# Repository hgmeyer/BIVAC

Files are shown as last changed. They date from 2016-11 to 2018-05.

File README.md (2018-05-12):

# BIVAC
While navigating their environments it is essential for autonomous mobile systems to actively avoid collisions with obstacles. Flying insects perform this behavioural task with ease relying mainly on information the visual system provides. BIVAC (Bio-Inspired Visual Avoidance of Collisions) is a low-cost collision avoidance system based on the extraction of nearness information from visual motion. The system allows an autonomous mobile agent to navigate in cluttered environments while actively avoiding obstacles.

**Please note:** This is the repository for a project that will be hosted on [hackaday.io](http://hackaday.io/). Please visit the [project page](https://hackaday.io/project/13301-bivac-bio-inspired-visual-collision-avoidance/) for more information.

<br />This work is licensed under a <a rel="license" href="http://creativecommons.org/licenses/by-sa/4.0/">Creative Commons Attribution-ShareAlike 4.0 International License</a>.

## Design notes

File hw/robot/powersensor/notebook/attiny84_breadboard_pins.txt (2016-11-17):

# I2C
SDA   -   E25
SCL   -   E26

# Digital
PB0   -   E27
PB1   -   E28

# Voltage measurement
12V   -   F25
5V    -   F26
3.3V  -   F27
1.8V  -   F28

# Current measurement
C_A   -   F29
C_B   -   F30

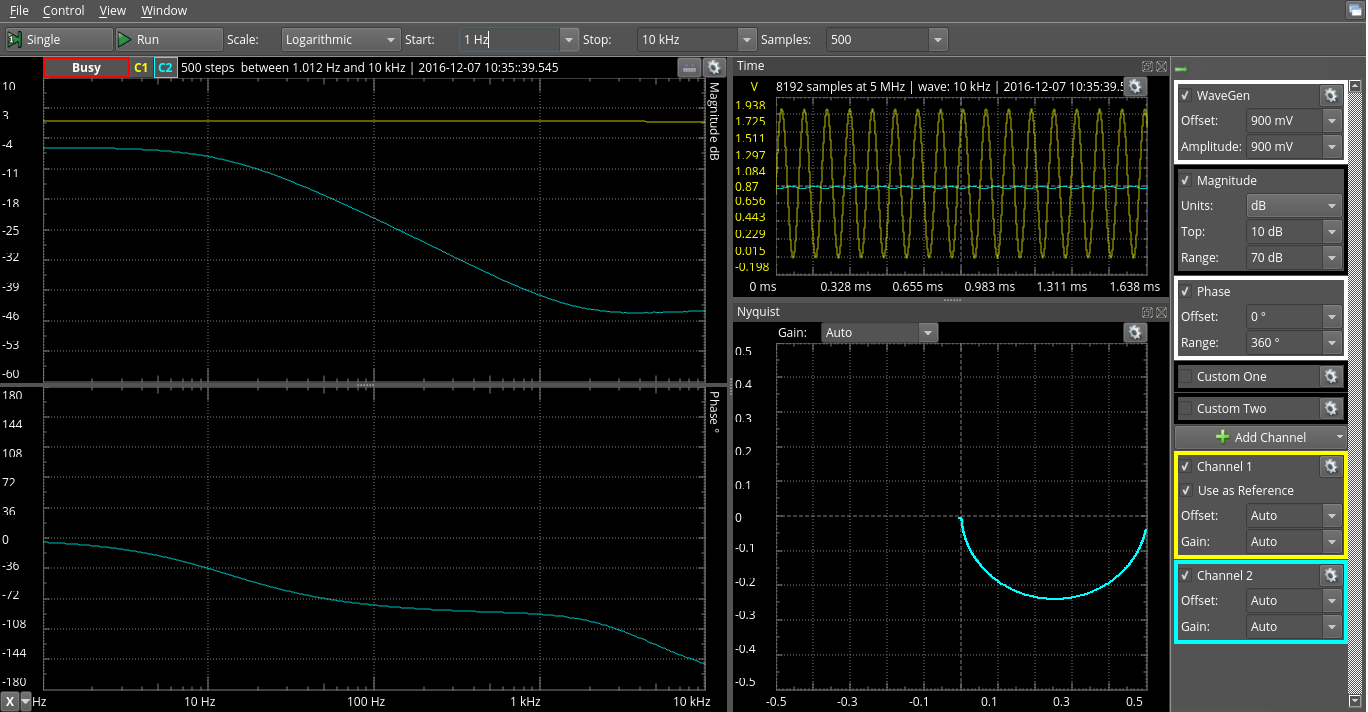
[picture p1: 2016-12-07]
hw/robot/powersensor/hw/analysis/input_stage.png

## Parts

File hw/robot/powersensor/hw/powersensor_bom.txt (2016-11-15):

Qty Value    Device             Package  Parts                Description                 PROD_ID (Reichelt)
5            M01PTH             1X01     J3, J4, J5, J6, J9   Header 1
1            M05PTH             1X05     J7                   Header 5
1            M06SILK_FEMALE_PTH 1X06     J8                   Header 6
1   1.8V     LED0603            LED-0603 D4                   LEDs                        LY L29K
1   100nF    CAP0603-CAP        0603-CAP C5                   Capacitor                   X7R-G0603 100N
4   10u      CAP0603-CAP        0603-CAP C1, C2, C3, C4       Capacitor                   GRM188R60J106ME47D (Conrad)
1   13k      RESISTOR0603-RES   0603-RES R1                   Resistor                    RND 0603 1 13K
5   1k1      RESISTOR0603-RES   0603-RES R2, R5, R8, R10, R11 Resistor                    RND 0603 1 1,1K
1   2k7      RESISTOR0603-RES   0603-RES R7                   Resistor                    RND 0603 1 2,7K
1   3.3V     LED0603            LED-0603 D3                   LEDs                        LO L29K
2   1k       RESISTOR0603-RES   0603-RES R17, R18             Resistor                    (optional)
1   4k7      RESISTOR0603-RES   0603-RES R4                   Resistor                    RND 0603 1 4,7K
1   5V       LED0603            LED-0603 D2                   LEDs                        LS L29K
4   750R     RESISTOR0603-RES   0603-RES R3, R6, R9, R12      Resistor                    RND 0603 1 750
1   ATTINY84 ATTINY84           SO14     U$1                  Atmel 14-pin 8kB flash uC   ATTINY 84A-SSU
1   I2C      PINHD-1X3/90       1X03/90  J2                   PIN HEADER
1   ISP      AVR_SPI_PRG_6PTH   2X3      J1                   AVR ISP 6 Pin
1   V_BAT    LED0603            LED-0603 D1                   LEDs                        LG L29K
1   560R     RESISTOR0603-RES   0603-RES R13                  Resistor                    SMD-0603 560
1   180R     RESISTOR0603-RES   0603-RES R14                  Resistor                    SMD-0603 180
1   82R      RESISTOR0603-RES   0603-RES R15                  Resistor                    SMD-0603 82
1   0R       RESISTOR0603-RES   0603-RES R16                  Resistor                    SMD-0603 0

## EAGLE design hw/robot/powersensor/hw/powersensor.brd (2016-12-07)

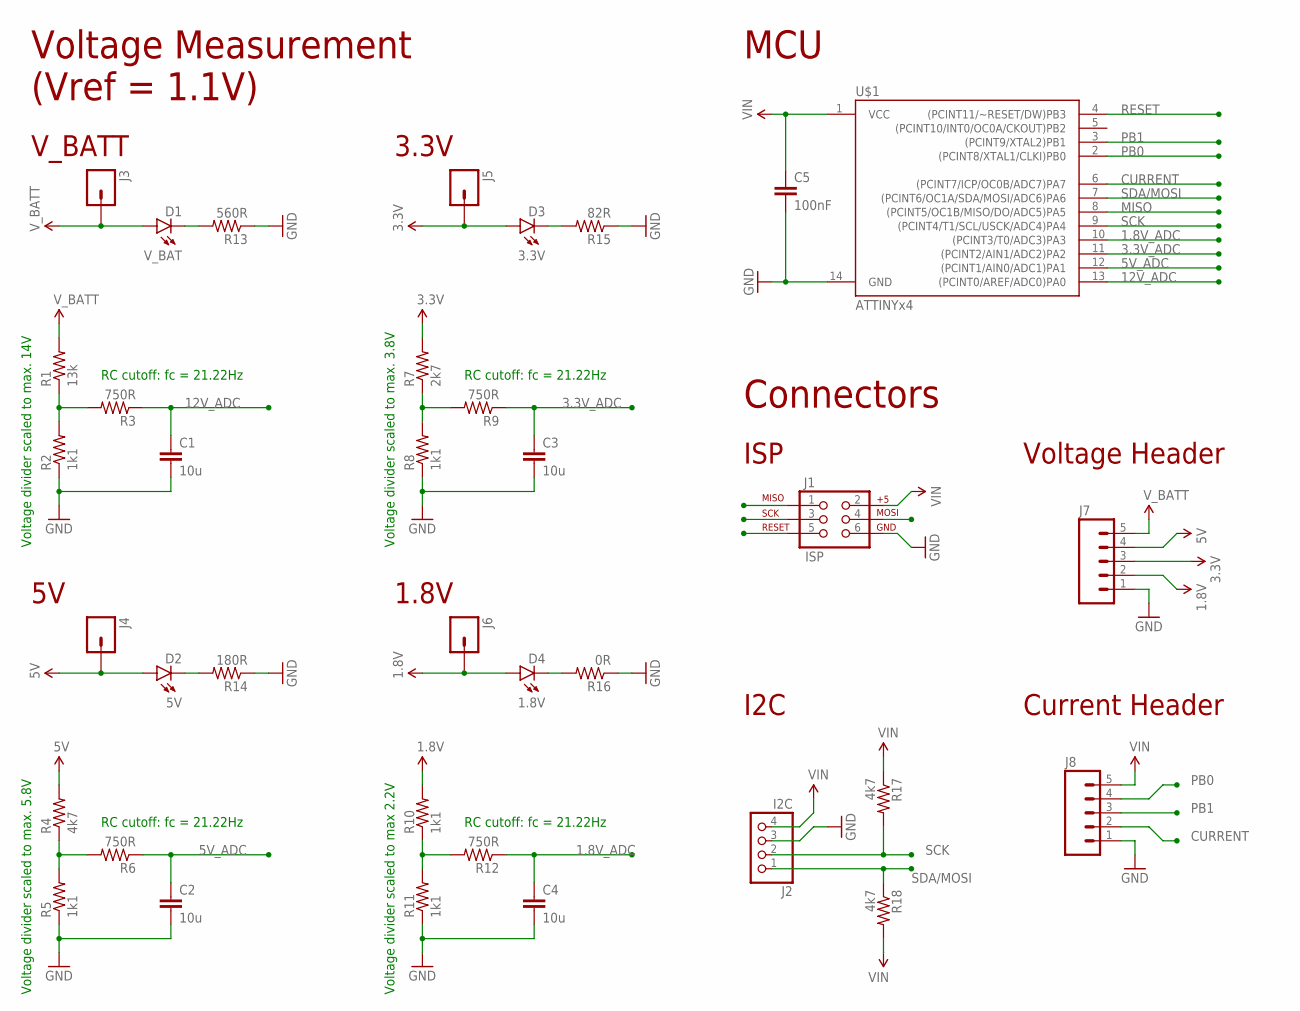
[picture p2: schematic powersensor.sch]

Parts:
C1, C2, C3, C4: 10u; 0603-CAP
C5: 100nF; 0603-CAP
D1: V_BAT; LED-0603
D2: 5V; LED-0603
D3: 3.3V; LED-0603
D4: 1.8V; LED-0603
J1: ISP; 2X3
J2: I2C; 1X04/90
J3, J4, J5, J6: M01PTH; 1X01
J7, J8: M05PTH; 1X05
R1: 13k; 0603-RES
R2, R5, R8, R10, R11: 1k1; 0603-RES
R3, R6, R9, R12: 750R; 0603-RES
R4, R17, R18: 4k7; 0603-RES
R7: 2k7; 0603-RES
R13: 560R; 0603-RES
R14: 180R; 0603-RES
R15: 82R; 0603-RES
R16: 0R; 0603-RES
U$1: ATTINYx4; SO14

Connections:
1.8V: D4.A, J6.1, J7.2, R10.2
1.8V_ADC: C4.1, R12.1, U$1.10 ((PCINT3/T0/ADC3)PA3)
3.3V: D3.A, J5.1, J7.3, R7.2
3.3V_ADC: C3.1, R9.1, U$1.11 ((PCINT2/AIN1/ADC2)PA2)
5V: D2.A, J4.1, J7.4, R4.2
5V_ADC: C2.1, R6.1, U$1.12 ((PCINT1/AIN0/ADC1)PA1)
12V_ADC: C1.1, R3.1, U$1.13 ((PCINT0/AREF/ADC0)PA0)
CURRENT: J8.2, U$1.6 ((PCINT7/ICP/OC0B/ADC7)PA7)
GND: C1.2, C2.2, C3.2, C4.2, C5.2, J1.6, J2.3, J7.1, J8.1, R2.1, R5.1, R8.1, R11.1, R13.1, R14.1, R15.1, R16.1, U$1.14 (GND)
MISO: J1.1, U$1.8 ((PCINT5/OC1B/MISO/DO/ADC5)PA5)
unnamed: R1.1, R2.2, R3.2
unnamed: R4.1, R5.2, R6.2
unnamed: R7.1, R8.2, R9.2
unnamed: R10.1, R11.2, R12.2
unnamed: D1.C, R13.2
unnamed: D2.C, R14.2
unnamed: D3.C, R15.2
unnamed: D4.C, R16.2
PB0: J8.4, U$1.2 ((PCINT8/XTAL1/CLKI)PB0)
PB1: J8.3, U$1.3 ((PCINT9/XTAL2)PB1)
RESET: J1.5, U$1.4 ((PCINT11/~RESET/DW)PB3)
SCK: J1.3, J2.2, R17.2, U$1.9 ((PCINT4/T1/SCL/USCK/ADC4)PA4)
SDA/MOSI: J1.4, J2.1, R18.1, U$1.7 ((PCINT6/OC1A/SDA/MOSI/ADC6)PA6)
VIN: C5.1, J1.2, J2.4, J8.5, R17.1, R18.2, U$1.1 (VCC)
V_BATT: D1.A, J3.1, J7.5, R1.2

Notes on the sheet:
Voltage divider scaled to max. 14V
Voltage divider scaled to max. 3.8V
Voltage divider scaled to max 2.2V
Voltage divider scaled to max. 5.8V
V_BATT
3.3V
1.8V
Voltage Measurement (Vref = 1.1V)
MCU
ISP
Connectors
I2C
Voltage Header
Current Header
RC cutoff: fc = 21.22Hz

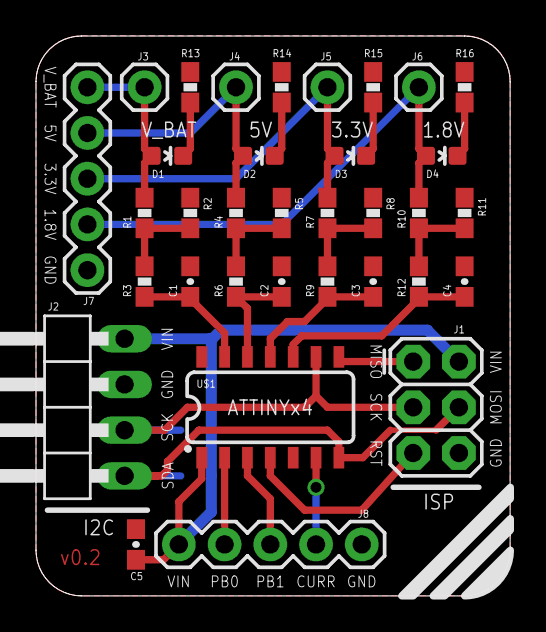
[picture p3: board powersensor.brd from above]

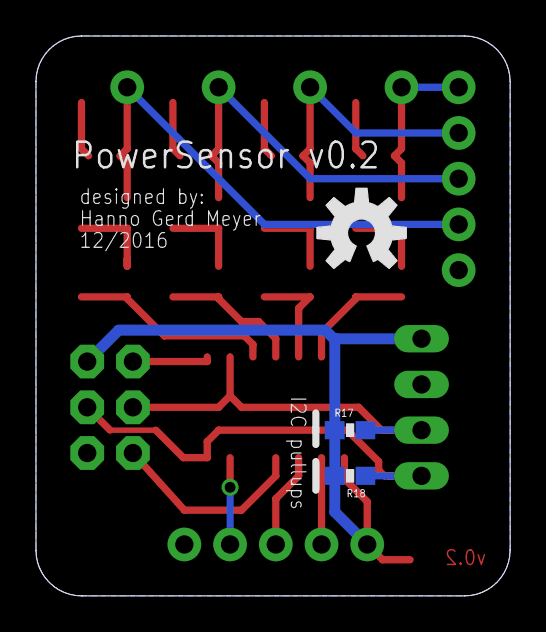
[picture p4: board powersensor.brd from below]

Board: 2 copper layers, 26.3 x 31.1 mm, 37 parts (3 on the bottom side), 25 nets.

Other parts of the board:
U$3: OSHW-LOGO-M

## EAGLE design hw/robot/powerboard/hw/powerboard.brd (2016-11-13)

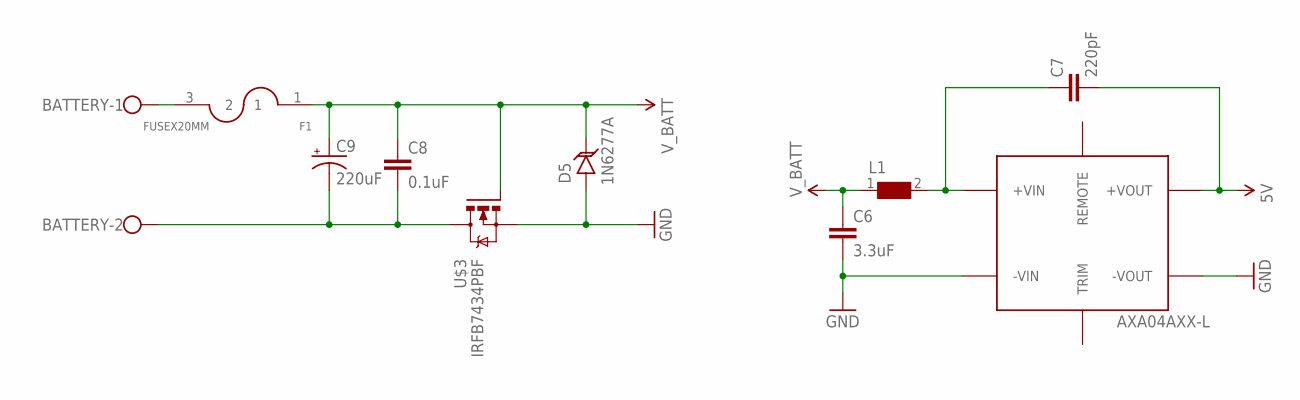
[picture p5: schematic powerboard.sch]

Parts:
BATTERY: W237-102
C6: 3.3uF; 1210
C7: 220pF; C1808
C8: 0.1uF; 0603-CAP
C9: 220uF; PANASONIC_G
D5: 1N6277A
F1: FUSEX20MM; FUSE_5MM
L1: WE-HCI-744314650_7030/7040/7050; WE-HCI_7030/7040/7050
U$2: AXA04AXX-L
U$3: IRFB7434PBF

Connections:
5V: C7.2, U$2.+VOUT
GND: C6.2, D5.A, U$2.-VIN, U$2.-VOUT, U$3.SOURCE (S)
unnamed: C7.1, L1.2, U$2.+VIN
unnamed: BATTERY.1, F1.3 (2)
unnamed: BATTERY.2, C8.2, C9.-, U$3.DRAIN (D)
V_BATT: C6.1, C8.1, C9.+, D5.C, F1.1, L1.1, U$3.GATE (G)

Board: 2 copper layers, 10 parts (0 on the bottom side), 6 nets, no tracks yet.

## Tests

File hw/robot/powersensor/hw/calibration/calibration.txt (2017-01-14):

5V transfer function:
8.755e-05 x + 0.0005361
a: 0.000536051312588, b: 8.75483919078e-05

3.3V transfer function:
5.727e-05 x - 0.00478
a: -0.00478023205199, b: 5.72741545385e-05

1.8V transfer function
3.297e-05 x + 0.008651
a: 0.00865060511459, b: 3.29668929132e-05

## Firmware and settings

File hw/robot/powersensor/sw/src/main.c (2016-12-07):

/*
 * PowerSensor v0.2 firmware
 * Copyright (C) 2016 Hanno Gerd Meyer <hanno@neuromail.de>
 *
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
 * You should have received a copy of the GNU General Public License along with
 * this program.  If not, see <http://www.gnu.org/licenses/>.
 */

#include <avr/io.h>
#include <avr/interrupt.h>
#include <util/delay.h>
#include <usiTwiSlave.h>

#ifndef DEBUG
#define DEBUG 0
#endif

// Define I2C adress of slave (Note: LSB is the I2C r/w flag and must not be used for addressing!)
#define SLAVE_ADDR  0b00001000  // 0x04

// The number of ADC channels to be multiplexed
#define ADC_N   5

// ADC channel and index variables
uint8_t adc_channels[ADC_N] = {0, 1, 2, 3, 7}; // PA0, PA1, PA2, PA3, PA7
uint8_t adc_index = 0;

// ADC buffer
uint16_t adc_buffer;
uint8_t adc_lowbyte;

void initTimer(void)
{
        // Set timer to CTC mode
        TCCR0A |= (1 << WGM01);

        // Set prescaler to 64
        TCCR0B |= (1 << CS01)|(1 << CS00);

        // Initialize counter
        TCNT0 = 0;

        // Set compare value corresponding to 500Hz (100Hz per Channel)
        OCR0A = 250;

        // Enable compare interrupt
        TIMSK0 |= (1 << OCIE0A);
}

void initADC(void)
{
        // Set reference voltage to 1.1V
        ADMUX |= (1 << REFS1);

        // Clear MUX0:5 and set adc channel according to current index
        ADMUX = (ADMUX & ~(0x3F)) | (adc_channels[adc_index] & 0x3F);

        // Enable ADC
        ADCSRA |= (1 << ADEN);

        // Set prescaler to 64 (125kHz)
        ADCSRA |= (1 << ADPS2) |
                  (1 << ADPS1);
}

ISR (TIM0_COMPA_vect)
{
        // Start ADC measurement
        ADCSRA |= (1 << ADSC);

        if(DEBUG) {
                // Toggle PB0
                PORTB ^= (1 << PB0);
        }
}

int main(void)
{

        if(DEBUG) {
                // Set PB0 and PB1 as output pins
                DDRB |= (1<<PB0) | (1<<PB1);
        }

        // Calibrate clock
        OSCCAL -= 0;

        // Disable interrupts
        cli();

        // Initialize timer
        initTimer();

        // Initialize ADC
        initADC();

        // Enable I2C slave
        usiTwiSlaveInit(SLAVE_ADDR);

        // Enable interrupts
        sei();

// Main loop
        while (1)
        {
                // If ADC measurement has been completed
                if ((ADCSRA & (1 << ADSC)) == 0)
                {
                        if (DEBUG) {
                                // Toggle PB1
                                PORTB ^= (1 << PB1);
                        }

                        // Get low byte of ADC measurement
                        adc_lowbyte = ADCL;

                        // Scale 10 Bit measurement to 16 Bit
                        adc_buffer = (ADCH << 8 | adc_lowbyte) * 64;

                        // Write ADC measurement to buffer
                        txbuffer[adc_index+adc_index] = adc_buffer;
                        txbuffer[adc_index+adc_index+1] = adc_buffer >> 8;

                        // Set ADC index
                        if (adc_index < ADC_N-1) {
                                adc_index += 1;
                        }
                        else{
                                adc_index = 0;
                        }

                        // Clear MUX0:5 and set ADC channel
                        ADMUX = (ADMUX & ~(0x3F)) | (adc_channels[adc_index] & 0x3F);

                        // Wait until next ADC measurement starts
                        while((ADCSRA & (1 << ADSC)) == 0) {}
                }
        }

        return 0;
}

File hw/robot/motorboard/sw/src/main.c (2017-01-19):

#include <avr/io.h>
#include <avr/interrupt.h>
#include <util/delay.h>
#include <usiTwiSlave.h>

// Define I2C adress of slave (Note: LSB is the I2C r/w flag and must not be used for addressing!)
#define SLAVE_ADDR  0b00001000  // 0x04

/* Initializes 16-Bit Timer1 for generating phase-correct PWM signal on OC1B pin */
void initPWMTimer(void){

        // * Set Timer1 to PWM mode 10: phase-correct, ICR1 defines top
        // * Clear OC1B on Compare Match when upcounting. Set OC1B on Compare Match when downcounting.
        // * Set prescaler to
        TCCR1A |= (1 << COM1B1) | (1 << WGM11);
        TCCR1B |= (1 << WGM13) | (1 << CS11) |(1 << CS10);

        // Set OC1B pin (PA5) as output
        DDRA  |= (1 << PA5);

        // Set Timer1 top to 16-bit MAX
        ICR1 = 0xFFFF;

        // Set duty cycle to 0%
        OCR1B = 0x0000;

        /*
           // TODO: Use 16-Bit timer1 for more fine-grained PWM control

           // Set OC0A (DDB2) as output pin
           DDRB = 1 << DDB2;

           // PWM mode 1: phase-correct, fixed top
           // Set OC0A on Compare Match when up-counting. Clear OC0A on compare Match when down-counting.
           TCCR0A = (1<<COM0A1) | (1<<COM0B0) | (1<<WGM00);

           // Set prescaler
           TCCR0B |= (1 << CS00);

           // Set duty cycle to 50%
           OCR0A = 0;
         */
}



void initSampleTimer(){
}

void setPWM(uint16_t pwm){
        OCR1B = pwm;
}

int main(void){
        // Disable interrupts
        cli();

        // Enable I2C slave
        usiTwiSlaveInit(SLAVE_ADDR);

        initPWMTimer();

        // Re-Enable interrupts
        sei();

        setPWM(0x00FF);

        while(1) {

        }
        return 0;
}

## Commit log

2016-10-21 Added data for E96 resistor values
    [E96_resistor_values.csv]
2016-10-21 Updated notebook for calculations on voltage dividers
2016-10-21 Modified voltage divider calculations to account for an internal reference voltage of 1.1V
2016-10-21 Initial commit of powerboard firmware
2016-10-21 Added section for current measurement in notebook
2016-10-25 Updated preliminary version of powerboard firmware
2016-10-26 Initial commit of EAGLE parts library for the powerboard
2016-10-26 Added datasheet of AXA04AXX-L DC/DC voltage regulator
2016-11-01 Changed powerboard project definition to use Attiny85 for testing purposes
2016-11-01 Recent progress with powerboard firmware
2016-11-03 Initial commit of powerboard schematics and board
    [powerboard.brd, powerboard.sch]
2016-11-04 Fixed AXA DC/DC module
    [powerboard.brd, powerboard.sch]
2016-11-05 Implemented preliminary switching between ADCs
2016-11-07 Recent progress with powerboard schematics
    [powerboard.brd, powerboard.sch]
2016-11-10 Added N-channel MOSFET and TVS-diode to powerboard
    [powerboard.brd, powerboard.sch]
2016-11-12 Initial commit of powerboard calibration script
2016-11-12 Added voltcraft submodule
2016-11-13 Initial commit of PowerSensor board. Decided to separate PowerBoard and PowerSensor.
    [powerboard.brd, powerboard.sch, powersensor.brd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]
2016-11-14 Added optional I2C pullups, broke out PB0/1 and performed some cosmetical changes to PowerSensor board
    [powersensor.brd, powersensor.sch]
2016-11-14 Added values and performed some cosmetic changes on PowerSensor schematics
    [powersensor.brd, powersensor.sch]
2016-11-14 Added preliminary powersensor BOM
2016-11-15 Fixed values and added product ids for PowerSensor BOM
    [powersensor.brd, powersensor.sch]
2016-11-15 Added PowerSensor package to custom library
    [powersensor.brd]
2016-11-22 Implemented voltage measurement and switched to ATtiny84 MCU
2016-11-22 Moved powersensor files into separate directories
    [powersensor.brd, powersensor.sch]
2016-11-22 Implemented differential current measurement and removed unneeded volatile variables
2016-12-07 Added analysis of powersensor input stage
    [input_stage.csv]
2016-12-07 Initial commit of PowerSensor v0.2
    [powersensor_v0.2.brd, powersensor_v0.2.sch]
2016-12-07 Added simple Arduino firmware for testing I2C output
2016-12-15 Added missing email address
    [SerialRX.py]
2016-12-19 Changed baud- and samplerate
2016-12-19 Added script for calibrating PowerSensor board
2016-12-19 Updated eagle library to account for changes on power sensor board
2016-12-19 Removed cruft
    [powersensor.brd, powersensor.sch, powersensor_v0.2.brd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]
2016-12-28 Read and show the complete sensorboard buffer
2017-01-14 Added calibration data
2017-01-16 Added Digilient Waveforms workbench for testing motor driver
2017-01-17 Refactored folder structure
    [E96_resistor_values.csv, input_stage.csv, powerboard.brd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]
2017-01-17 Initial commit of motorboard firmware
2017-01-19 Fixed 16-Bit PWM signal generation
    [main.c]

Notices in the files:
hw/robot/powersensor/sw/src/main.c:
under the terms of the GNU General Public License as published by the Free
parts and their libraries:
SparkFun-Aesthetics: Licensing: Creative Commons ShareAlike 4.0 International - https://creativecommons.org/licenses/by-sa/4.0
